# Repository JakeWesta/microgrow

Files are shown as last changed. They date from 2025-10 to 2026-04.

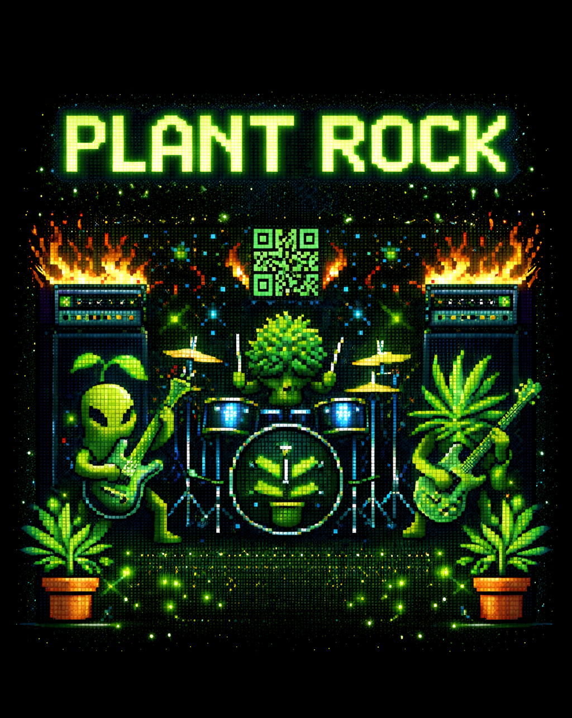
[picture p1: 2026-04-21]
app/assets/sprites/Rock_Poster.png

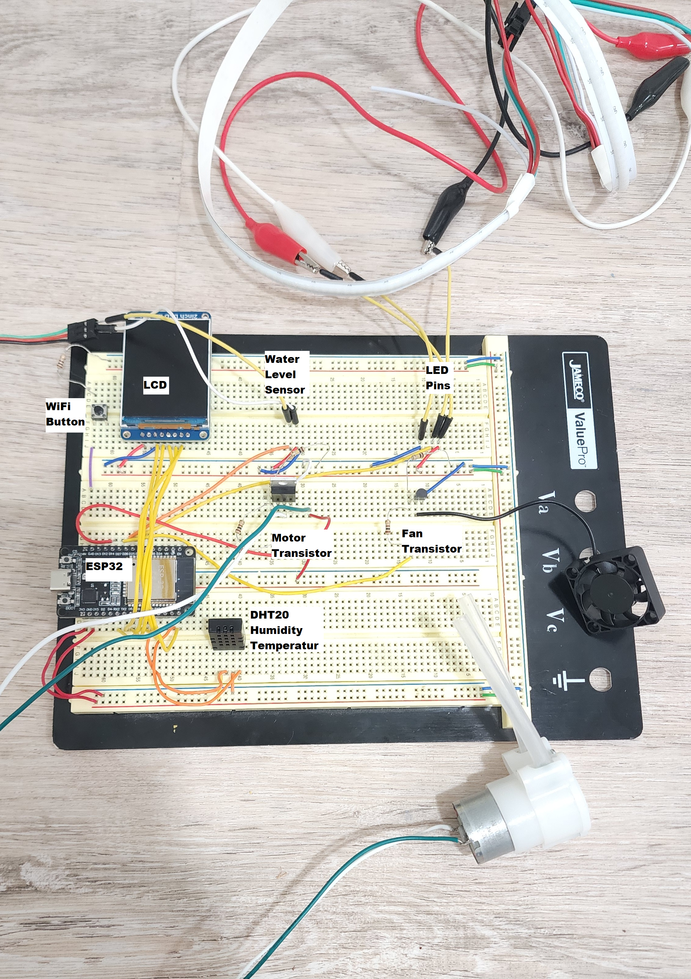
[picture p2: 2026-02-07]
Documentation/PCB 1.0/prototype_wiring_photo.png

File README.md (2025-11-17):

# Micro-Grow

- Flutter app demo video: https://www.youtube.com/watch?v=zIg6AqKC-sg

## Implemented Features:
### Pre-Alpha Build:
- **MQTT Connection** - Set up two-way communication between the ESP32 and the mobile app by using the MQTT protocol and EMQX broker.
- **Data Management** - Handle the storing of data by using a Hive database, which stores the watering cycle for each microgreen type.
- **Real-Time Sensor Data** - Configured ESP32 to poll readings from DHT11 temperature sensor and publishes the data every 5 seconds to the MQTT topic `microgrow/<habitatID>/sensor`.
- **User Interface** - Developed a Flutter app using Dart to allow the user to initialize and manage their MicroGrow habitat. Clicking on the habitat will display the real-time sensor data from the DHT11 on the app interface.

### Design Prototype:
- **Expanded Sensor Data** - Updated ESP32 code to publish sensor data for temperature/humidity, water level, and light intensity to MQTT topics `microgrow/<habitatID>/temp, humidity, water, light`. Sensor data is visible on the LCD screen to allow the user to easily monitor environmental conditions without their mobile device.
- **Expanded User Interface** - Updated dashboard to displays multiple created habitats and implemented the option to add and remove them. Selecting a habitat will display the real-time sensor data readings sent from the ESP32 for temperature, humidity, water level, and light intensity. Implemented the 'fun area' for the user to interact with their plant character
- **Schedule-Based Automation** - ESP32 pumps water from the water reservoir to the watering tray based on the watering schedule information sent during `microgrow/init`.
- **Manual Override** - Added a method for the user to control the water pump, fans, and light intensity manually from within the app. This feature does not interfere with the schedule timing.
- **Hardware** - Determined pin assignments for each electrical component. Connected ESP32, sensors, pump, lights, and LCD screen on a breadboard to test the functionality of each system. Designed CAD models to 3D-print the chassis and parts for the MicroGrow unit.

## Future Improvements:
- Include misting pump to regulate humidity within the habitat
- Create pixelated character sprites to display on the LCD screen
- Expand the 'fun area' in the mobile app to include customization features and scripted interaction between characters

## How to Use:

### Requirements:
- Flutter SDK
- Dart
- VS Code
- Arduino IDE
- Hive (for database)
- EMQX MQTT broker

### To setup the mobile application:
1. Ensure the required software is installed and install the necessary dependencies
2. Launch the mobile application:
   - Open VS Code and clone the repository
   - If prompted on VS Code, install the Flutter SDK and add to path if missing.
   - Install Flutter and Dart VS Code exstentions
   - Navigate to the app directory with `cd microgrow/app`
   - Fetch packages with `flutter pub get`
   - Connect to a 2.4 GHz WiFi network, such as a mobile hotspot
   - Start the application with `flutter run -d windows`
3. Flash the ESP32 firmware:
   - Open `main.ino` from the `ESP32 Firmware` directory in the Arduino IDE
   - Connect the ESP32 to a USB port on your computer
   - Follow the tutorial for the IDE to recognize the board: https://randomnerdtutorials.com/installing-the-esp32-board-in-arduino-ide-windows-instructions/
   - In Arduino IDE, select the correct configuration:
     - Board: ESP32 Dev Module
     - Port: auto-detected when plugging in
4. You may need to install the following packages. Easiest way is to go to the library manager tab on the left and search:
   - **PubSubClient** by Nick O'Leary
   - **DHT20** by Rob Tilaart
   - **ArduinoJson** by Benoit Blanchon
   - **Adafruit GFX Library** by Adafruit
   - **Adafruit ST7735 and ST7789 Library** by Adafruit
   - **FastLED** by Daniel Garcia
6. At the top of the code, assign the corresponding network information to the variables `ssid` and `password`
7. Press Upload and wait for flashing to complete

## Known Bugs:
- If sensor is unplugged, it displays garbage values. We don't handle that issue, as it displays more than 7 digits when disconnected from ESP32.
- If there is a disconnect from MQTT, we don't test for reconnection.
- Sometimes the ESP32 flashing will fail if its GPIO pins are connected to external peripherals/sensors. Remove the ESP32 from the breadboard before flashing to resolve this.
- Pump and fan will sometimes stop working during regular use.
- The current setup for the init sequence sends a JSON that is too large for the ESP32 to parse. This means that light scheduling is currently not being sent, as it had to be trimmed for the JSON to fit.

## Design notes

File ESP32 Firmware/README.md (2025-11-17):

# To run the ESP32 firmware:

1. Install the open-source Arduino IDE
2. Follow the tutorial for the IDE to recognize the board: https://randomnerdtutorials.com/installing-the-esp32-board-in-arduino-ide-windows-instructions/
3. Install the following packages. Easiest way is to go to the library manager tab on the left and search:
	
	PubSubClient by Nick O'Leary
	
	DHT20 by Rob Tilaart
	
	ArduinoJson by Benoit Blanchon
	
	Adafruit GFX Library by Adafruit
	
	Adafruit ST7735 and ST7789 Library by Adafruit
	
	FastLED by Daniel Garcia
4. Upload the firmware

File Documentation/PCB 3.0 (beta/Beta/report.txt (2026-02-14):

Info: Processing symbol 'DHT1:Connector_Molex:Molex_Micro-Fit_3.0_43650-0400_1x04_P3.00mm_Horizontal'.
Info: Processing symbol 'R1:Resistor_SMD:R_0201_0603Metric'.
Info: Processing symbol 'Q3:Package_TO_SOT_THT:TO-220-3_Vertical'.
Info: Processing symbol 'R3:Resistor_SMD:R_0201_0603Metric'.
Info: Processing symbol 'ST7789V1:Connector_Molex:Molex_Micro-Fit_3.0_43650-0600_1x06_P3.00mm_Horizontal'.
Info: Processing symbol 'Water_Level_Sensor1:Connector_Molex:Molex_Micro-Fit_3.0_43650-0300_1x03_P3.00mm_Horizontal'.
Info: Total warnings: 18, errors: 19.
Info: Processing symbol 'M1:Connector_Molex:Molex_Micro-Fit_3.0_43650-0215_1x02_P3.00mm_Vertical'.
Info: Processing symbol 'U1:esp32_devkit_v1_doit:esp32_devkit_v1_doit'.
Info: Processing symbol 'SW1:Connector_Molex:Molex_Micro-Fit_3.0_43650-0215_1x02_P3.00mm_Vertical'.
Info: Processing symbol 'Perilstatic_Pump1:Connector_Molex:Molex_Micro-Fit_3.0_43650-0215_1x02_P3.00mm_Vertical'.
Info: Processing symbol 'LED_STRIP1:Connector_Molex:Molex_Micro-Fit_3.0_43650-0300_1x03_P3.00mm_Horizontal'.
Info: Processing symbol 'Q1:Package_TO_SOT_THT:TO-220-3_Vertical'.
Info: Processing symbol 'R4:Resistor_SMD:R_0201_0603Metric'.
Info: Processing symbol 'R2:Resistor_SMD:R_0201_0603Metric'.
Added DHT1 (footprint 'Connector_Molex:Molex_Micro-Fit_3.0_43650-0400_1x04_P3.00mm_Horizontal').
Changed REF** reference designator to DHT1.
Changed DHT1 value from Molex_Micro-Fit_3.0_43650-0400_1x04_P3.00mm_Horizontal to ~.
Updated DHT1 symbol association from  to /6e4c08a4-b1cd-4914-aef5-b97c3696f05f.
Updated DHT1 sheetname to '/'.
Updated DHT1 sheetfile to 'prototype.kicad_sch'.
Updated Water_Level_Sensor1 sheetname to '/'.
Updated Water_Level_Sensor1 sheetfile to 'prototype.kicad_sch'.

Added LED_STRIP1 (footprint 'Connector_Molex:Molex_Micro-Fit_3.0_43650-0300_1x03_P3.00mm_Horizontal').
Changed REF** reference designator to LED_STRIP1.
Changed LED_STRIP1 value from Molex_Micro-Fit_3.0_43650-0300_1x03_P3.00mm_Horizontal to ~.
Updated LED_STRIP1 symbol association from  to /8e498da7-6c69-4450-a1d9-924dce50ed07.
Updated LED_STRIP1 sheetname to '/'.
Updated LED_STRIP1 sheetfile to 'prototype.kicad_sch'.
Changed REF** reference designator to Water_Level_Sensor1.
Added M1 (footprint 'Connector_Molex:Molex_Micro-Fit_3.0_43650-0215_1x02_P3.00mm_Vertical').
Changed REF** reference designator to M1.
Changed M1 value from Molex_Micro-Fit_3.0_43650-0215_1x02_P3.00mm_Vertical to Fan.
Updated M1 symbol association from  to /a24ab250-104e-40cc-be6c-cd05863d6f31.
Updated M1 fields.
Updated M1 sheetname to '/'.
Updated M1 sheetfile to 'prototype.kicad_sch'.
Add net /FAN_NEG.
Connected M1 pin 2 to /FAN_NEG.
Add net VCC.
Connected M1 pin 1 to VCC.
Added Perilstatic_Pump1 (footprint 'Connector_Molex:Molex_Micro-Fit_3.0_43650-0215_1x02_P3.00mm_Vertical').
Changed REF** reference designator to Perilstatic_Pump1.
Changed Perilstatic_Pump1 value from Molex_Micro-Fit_3.0_43650-0215_1x02_P3.00mm_Vertical to ~.
Updated Perilstatic_Pump1 symbol association from  to /13c4dc11-f264-4864-8656-4de5b2fcf814.
Updated Perilstatic_Pump1 sheetname to '/'.
Updated Perilstatic_Pump1 sheetfile to 'prototype.kicad_sch'.
Added Q1 (footprint 'Package_TO_SOT_THT:TO-220-3_Vertical').
Changed REF** reference designator to Q1.
Changed Q1 value from TO-220-3_Vertical to IRLB8721PBF.
Updated Q1 symbol association from  to /b185a6f1-6a33-459d-a671-ce34d81b2ea3.
Updated Q1 fields.
Updated Q1 sheetname to '/'.
Updated Q1 sheetfile to 'prototype.kicad_sch'.
Updated Q1 footprint filters to 'TO?220*'.
Add net GND.
Connected Q1 pin 3 to GND.
Add net /PUMP_NEG.
Connected Q1 pin 2 to /PUMP_NEG.
Add net Net-(Q1-G).
Connected Q1 pin 1 to Net-(Q1-G).
Updated M1 footprint filters to 'PinHeader*P2.54mm* TerminalBlock*'.
Added Q3 (footprint 'Package_TO_SOT_THT:TO-220-3_Vertical').
Changed REF** reference designator to Q3.
Changed Q3 value from TO-220-3_Vertical to IRLB8721PBF.
Updated Q3 symbol association from  to /fbe2aa08-65bc-4db5-b509-0606b8fdc2ba.
Updated Q3 fields.
Updated Q3 sheetname to '/'.
Updated Q3 sheetfile to 'prototype.kicad_sch'.
Updated Q3 footprint filters to 'TO?220*'.
Add net Net-(Q3-G).
Connected Q3 pin 1 to Net-(Q3-G).
Connected Q3 pin 2 to /FAN_NEG.
Connected Q3 pin 3 to GND.
Added R1 (footprint 'Resistor_SMD:R_0201_0603Metric').
Changed REF** reference designator to R1.
Changed R1 value from R_0201_0603Metric to 100.
Updated R1 symbol association from  to /6cbc41ab-6199-446f-b66f-0273e11d1e1b.
Updated R1 fields.
Updated R1 sheetname to '/'.
Updated R1 sheetfile to 'prototype.kicad_sch'.
Updated R1 footprint filters to 'R_*'.
Add net /PUMP.
Connected R1 pin 2 to /PUMP.
Connected R1 pin 1 to Net-(Q1-G).
Added R2 (footprint 'Resistor_SMD:R_0201_0603Metric').
Changed REF** reference designator to R2.
Changed R2 value from R_0201_0603Metric to 100k.
Updated R2 symbol association from  to /58fef6ab-5448-4966-9282-118c6e4f16f3.
Updated R2 sheetname to '/'.
Updated R2 sheetfile to 'prototype.kicad_sch'.
Updated R2 footprint filters to 'R_*'.
Connected R2 pin 1 to GND.
Connected R2 pin 2 to Net-(Q1-G).
Added R3 (footprint 'Resistor_SMD:R_0201_0603Metric').
Changed REF** reference designator to R3.
Changed R3 value from R_0201_0603Metric to 100.
Updated R3 symbol association from  to /cc2fe59e-3a58-4862-b4cd-096af761090b.
Updated R3 fields.
Updated R3 sheetname to '/'.
Updated R3 sheetfile to 'prototype.kicad_sch'.
Updated R3 footprint filters to 'R_*'.
Connected R3 pin 2 to Net-(Q3-G).
Add net /FAN.
Connected R3 pin 1 to /FAN.
Added R4 (footprint 'Resistor_SMD:R_0201_0603Metric').
Changed REF** reference designator to R4.
Changed R4 value from R_0201_0603Metric to 100k.
Updated R4 symbol association from  to /ef9e54ad-bc10-445a-8cc7-7e4a79940005.
Updated R4 fields.
Updated R4 sheetname to '/'.
Updated R4 sheetfile to 'prototype.kicad_sch'.
Updated R4 footprint filters to 'R_*'.
Connected R4 pin 2 to GND.
Connected R4 pin 1 to Net-(Q3-G).
Updated R2 fields.
Added ST7789V1 (footprint 'Connector_Molex:Molex_Micro-Fit_3.0_43650-0600_1x06_P3.00mm_Horizontal').
Changed REF** reference designator to ST7789V1.
Changed ST7789V1 value from Molex_Micro-Fit_3.0_43650-0600_1x06_P3.00mm_Horizontal to ~.
Updated ST7789V1 symbol association from  to /6443309b-f941-4119-b5bf-95145ad43db5.
Updated ST7789V1 sheetname to '/'.
Updated ST7789V1 sheetfile to 'prototype.kicad_sch'.
Added SW1 (footprint 'Connector_Molex:Molex_Micro-Fit_3.0_43650-0215_1x02_P3.00mm_Vertical').
Changed REF** reference designator to SW1.
Changed SW1 value from Molex_Micro-Fit_3.0_43650-0215_1x02_P3.00mm_Vertical to SW_Push.
Updated SW1 symbol association from  to /d7c7dc86-ded3-42bf-bfc8-d6a93b28d2ff.
Updated SW1 fields.
Updated SW1 sheetname to '/'.
Updated SW1 sheetfile to 'prototype.kicad_sch'.
Add net /WiFi_BUTTON.
Connected SW1 pin 1 to /WiFi_BUTTON.
Connected SW1 pin 2 to GND.
Added U1 (footprint 'esp32_devkit_v1_doit:esp32_devkit_v1_doit').
Changed REF** reference designator to U1.
Changed U1 value from ESP32-DevKit-V1-DOIT to ESP32-DEVKIT-V1.
Updated U1 symbol association from  to /7857917b-6d23-4520-a81d-1aefb2627a26.
Updated U1 fields.
Updated U1 sheetname to '/'.
Updated U1 sheetfile to 'prototype.kicad_sch'.
Add net /LCD_DC.
Connected U1 pin 6 to /LCD_DC.
Add net /DHT_SDA.
Connected U1 pin 11 to /DHT_SDA.
Add net +3V3.
Connected U1 pin 30 to +3V3.
Add net /LCD_CLK.
Connected U1 pin 9 to /LCD_CLK.
Add net unconnected-(U1-D4-Pad5).
Connected U1 pin 5 to unconnected-(U1-D4-Pad5).
Add net /LCD_RST.
Connected U1 pin 7 to /LCD_RST.
Connected U1 pin 1 to VCC.
Add net /LED_STRIP.
Connected U1 pin 25 to /LED_STRIP.
Add net unconnected-(U1-D33-Pad22).
Connected U1 pin 22 to unconnected-(U1-D33-Pad22).
Add net /WATER_LEV.
Connected U1 pin 26 to /WATER_LEV.
Connected U1 pin 2 to GND.
Add net unconnected-(U1-D35-Pad20).
Connected U1 pin 20 to unconnected-(U1-D35-Pad20).
Add net unconnected-(U1-D34-Pad19).
Connected U1 pin 19 to unconnected-(U1-D34-Pad19).
Connected U1 pin 29 to GND.
Add net unconnected-(U1-VP-Pad17).
Connected U1 pin 17 to unconnected-(U1-VP-Pad17).
Connected U1 pin 13 to unconnected-(U1-TX0-Pad13).
Add net unconnected-(U1-D25-Pad23).
Connected U1 pin 23 to unconnected-(U1-D25-Pad23).
Connected U1 pin 24 to /FAN.
Add net unconnected-(U1-EN-Pad16).
Connected U1 pin 16 to unconnected-(U1-EN-Pad16).
Add net unconnected-(U1-D19-Pad10).
Connected U1 pin 10 to unconnected-(U1-D19-Pad10).
Add net unconnected-(U1-VN-Pad18).
Connected U1 pin 18 to unconnected-(U1-VN-Pad18).
Add net /LCD_CS.
Connected U1 pin 8 to /LCD_CS.
Add net /LCD_DIN.
Connected U1 pin 15 to /LCD_DIN.
Add net unconnected-(U1-D13-Pad28).
Connected U1 pin 28 to unconnected-(U1-D13-Pad28).
Add net unconnected-(U1-D12-Pad27).
Connected U1 pin 27 to unconnected-(U1-D12-Pad27).
Add net unconnected-(U1-RX0-Pad12).
Connected U1 pin 12 to unconnected-(U1-RX0-Pad12).
Connected U1 pin 21 to /PUMP.
Add net /DHT_SCL.
Connected U1 pin 14 to /DHT_SCL.
Connected U1 pin 4 to /WiFi_BUTTON.
Add net unconnected-(U1-D15-Pad3).
Connected U1 pin 3 to unconnected-(U1-D15-Pad3).
Added Water_Level_Sensor1 (footprint 'Connector_Molex:Molex_Micro-Fit_3.0_43650-0300_1x03_P3.00mm_Horizontal').
Add net unconnected-(U1-TX0-Pad13).
Changed Water_Level_Sensor1 value from Molex_Micro-Fit_3.0_43650-0300_1x03_P3.00mm_Horizontal to ~.
Updated Water_Level_Sensor1 symbol association from  to /28ca019c-f3e1-41e0-b59c-fe60d403124b.
Warning: No net found for component DHT1 pad 4 (no pin 4 in symbol).
Warning: No net found for component DHT1 pad 3 (no pin 3 in symbol).
Warning: No net found for component DHT1 pad 1 (no pin 1 in symbol).
Warning: No net found for component DHT1 pad 2 (no pin 2 in symbol).
Warning: No net found for component LED_STRIP1 pad 3 (no pin 3 in symbol).
Warning: No net found for component LED_STRIP1 pad 2 (no pin 2 in symbol).
Warning: No net found for component LED_STRIP1 pad 1 (no pin 1 in symbol).
Warning: No net found for component ST7789V1 pad 2 (no pin 2 in symbol).
Warning: No net found for component Perilstatic_Pump1 pad 1 (no pin 1 in symbol).
Warning: No net found for component ST7789V1 pad 5 (no pin 5 in symbol).
Warning: No net found for component ST7789V1 pad 1 (no pin 1 in symbol).
Warning: No net found for component ST7789V1 pad 6 (no pin 6 in symbol).
Warning: No net found for component Water_Level_Sensor1 pad 2 (no pin 2 in symbol).
Warning: No net found for component Water_Level_Sensor1 pad 1 (no pin 1 in symbol).
Warning: No net found for component Water_Level_Sensor1 pad 3 (no pin 3 in symbol).
Warning: No net found for component ST7789V1 pad 4 (no pin 4 in symbol).
Warning: No net found for component Perilstatic_Pump1 pad 2 (no pin 2 in symbol).
Warning: No net found for component ST7789V1 pad 3 (no pin 3 in symbol).
Error: Symbol DHT1 has pins with no number.  These pins can not be matched to pads in Connector_Molex:Molex_Micro-Fit_3.0_43650-0400_1x04_P3.00mm_Horizontal.
Error: Symbol DHT1 has pins with no number.  These pins can not be matched to pads in Connector_Molex:Molex_Micro-Fit_3.0_43650-0400_1x04_P3.00mm_Horizontal.
Error: Symbol DHT1 has pins with no number.  These pins can not be matched to pads in Connector_Molex:Molex_Micro-Fit_3.0_43650-0400_1x04_P3.00mm_Horizontal.
Error: Symbol LED_STRIP1 has pins with no number.  These pins can not be matched to pads in Connector_Molex:Molex_Micro-Fit_3.0_43650-0300_1x03_P3.00mm_Horizontal.
Error: Symbol Perilstatic_Pump1 has pins with no number.  These pins can not be matched to pads in Connector_Molex:Molex_Micro-Fit_3.0_43650-0215_1x02_P3.00mm_Vertical.
Error: Symbol Perilstatic_Pump1 has pins with no number.  These pins can not be matched to pads in Connector_Molex:Molex_Micro-Fit_3.0_43650-0215_1x02_P3.00mm_Vertical.
Error: Symbol ST7789V1 has pins with no number.  These pins can not be matched to pads in Connector_Molex:Molex_Micro-Fit_3.0_43650-0600_1x06_P3.00mm_Horizontal.
Error: Symbol ST7789V1 has pins with no number.  These pins can not be matched to pads in Connector_Molex:Molex_Micro-Fit_3.0_43650-0600_1x06_P3.00mm_Horizontal.
Error: Symbol ST7789V1 has pins with no number.  These pins can not be matched to pads in Connector_Molex:Molex_Micro-Fit_3.0_43650-0600_1x06_P3.00mm_Horizontal.
Error: Symbol ST7789V1 has pins with no number.  These pins can not be matched to pads in Connector_Molex:Molex_Micro-Fit_3.0_43650-0600_1x06_P3.00mm_Horizontal.
Error: Symbol ST7789V1 has pins with no number.  These pins can not be matched to pads in Connector_Molex:Molex_Micro-Fit_3.0_43650-0600_1x06_P3.00mm_Horizontal.
Error: Symbol ST7789V1 has pins with no number.  These pins can not be matched to pads in Connector_Molex:Molex_Micro-Fit_3.0_43650-0600_1x06_P3.00mm_Horizontal.
Error: Symbol ST7789V1 has pins with no number.  These pins can not be matched to pads in Connector_Molex:Molex_Micro-Fit_3.0_43650-0600_1x06_P3.00mm_Horizontal.
Error: Symbol Water_Level_Sensor1 has pins with no number.  These pins can not be matched to pads in Connector_Molex:Molex_Micro-Fit_3.0_43650-0300_1x03_P3.00mm_Horizontal.
Error: Symbol Water_Level_Sensor1 has pins with no number.  These pins can not be matched to pads in Connector_Molex:Molex_Micro-Fit_3.0_43650-0300_1x03_P3.00mm_Horizontal.
Error: Symbol Water_Level_Sensor1 has pins with no number.  These pins can not be matched to pads in Connector_Molex:Molex_Micro-Fit_3.0_43650-0300_1x03_P3.00mm_Horizontal.
Error: Symbol LED_STRIP1 has pins with no number.  These pins can not be matched to pads in Connector_Molex:Molex_Micro-Fit_3.0_43650-0300_1x03_P3.00mm_Horizontal.
Error: Symbol LED_STRIP1 has pins with no number.  These pins can not be matched to pads in Connector_Molex:Molex_Micro-Fit_3.0_43650-0300_1x03_P3.00mm_Horizontal.
Error: Symbol DHT1 has pins with no number.  These pins can not be matched to pads in Connector_Molex:Molex_Micro-Fit_3.0_43650-0400_1x04_P3.00mm_Horizontal.

Info: Total warnings: 18, errors: 19.

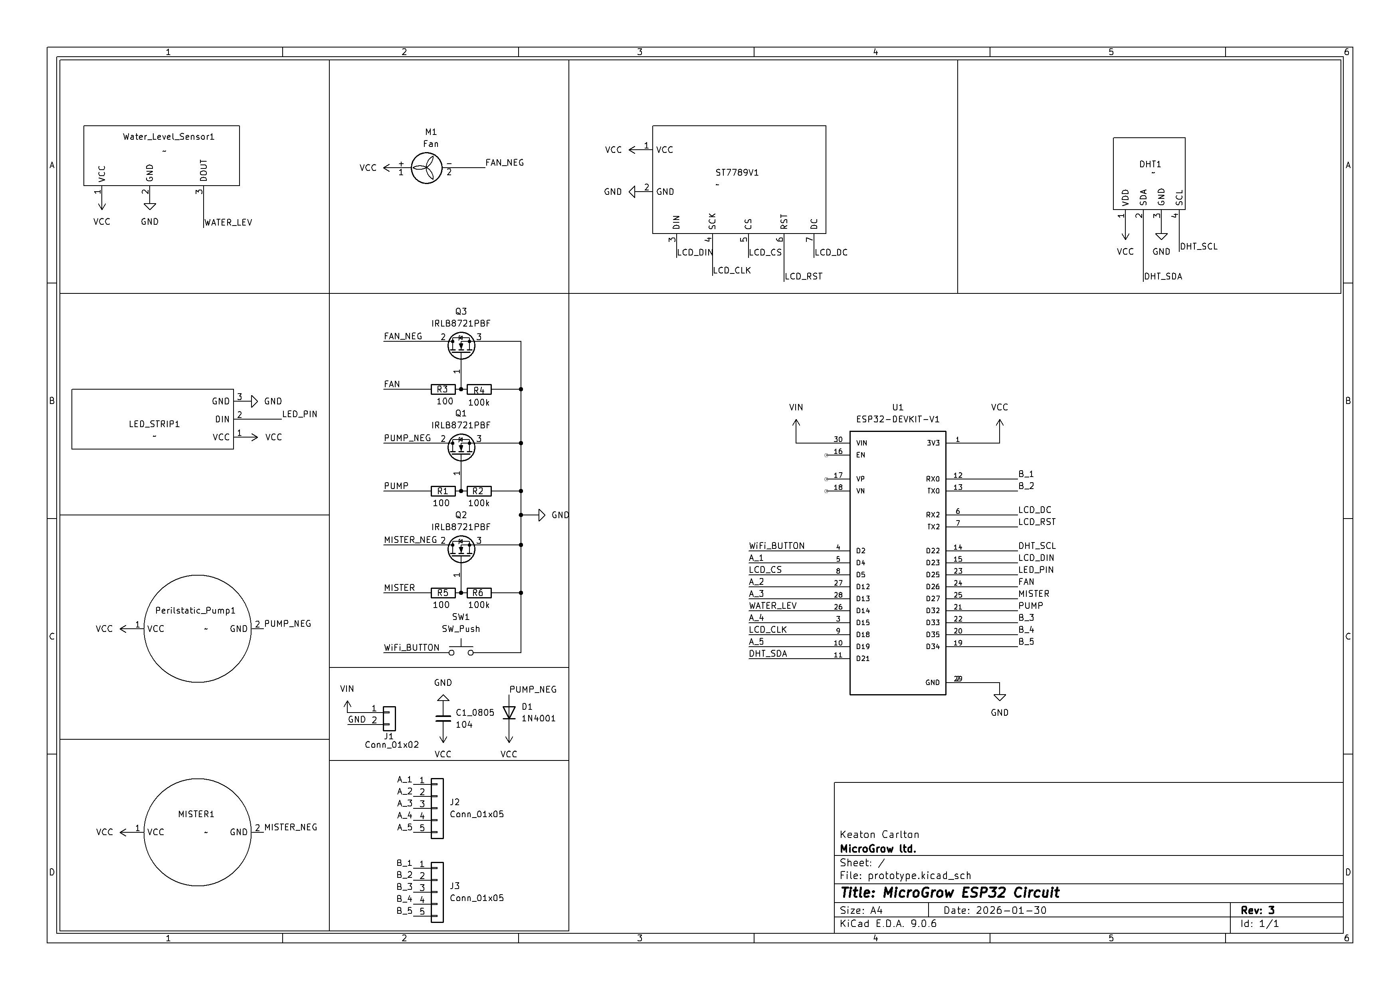
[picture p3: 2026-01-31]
Documentation/PCB 1.0/schematic_photo.png

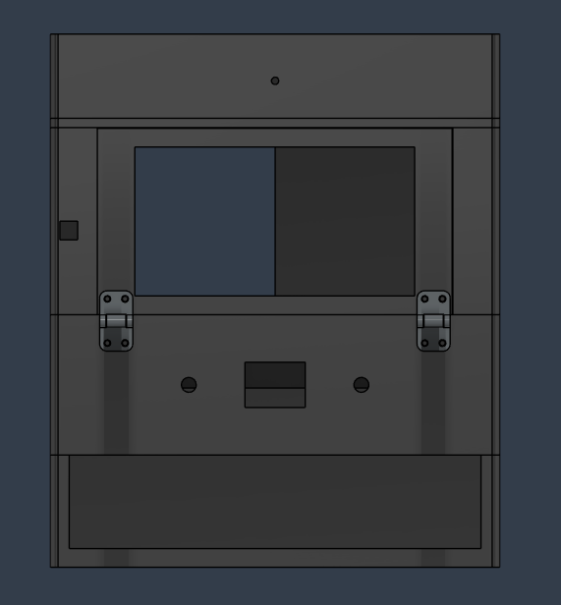
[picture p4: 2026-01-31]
Physical Design/Final Front View.PNG

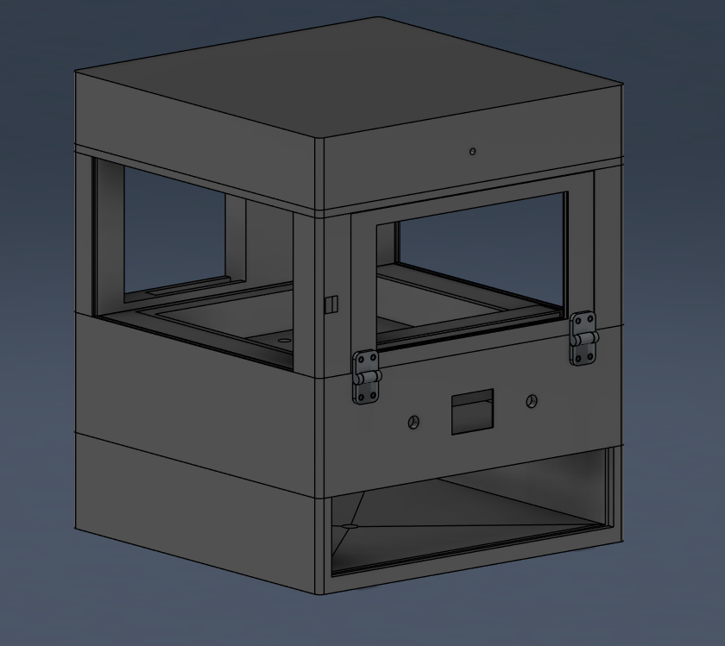
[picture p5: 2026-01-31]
Physical Design/Final Ortho View.PNG

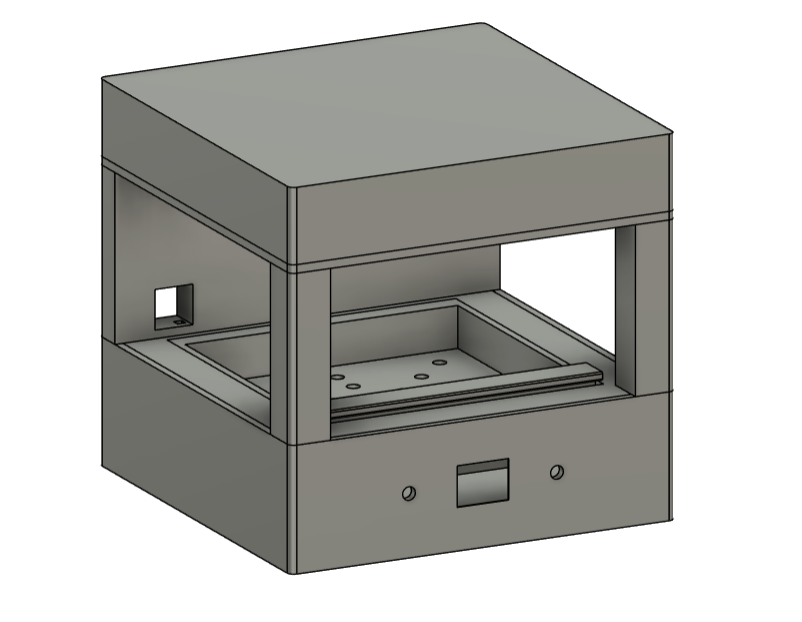
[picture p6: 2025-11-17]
Physical Design/MicroGrow 3D Model.png

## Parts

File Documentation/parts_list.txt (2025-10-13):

https://docs.google.com/spreadsheets/d/1zEimQMvjbTs6dZiR2b9LwuBSMXzHEefUJ1ij9qsu0_o/edit?usp=sharing

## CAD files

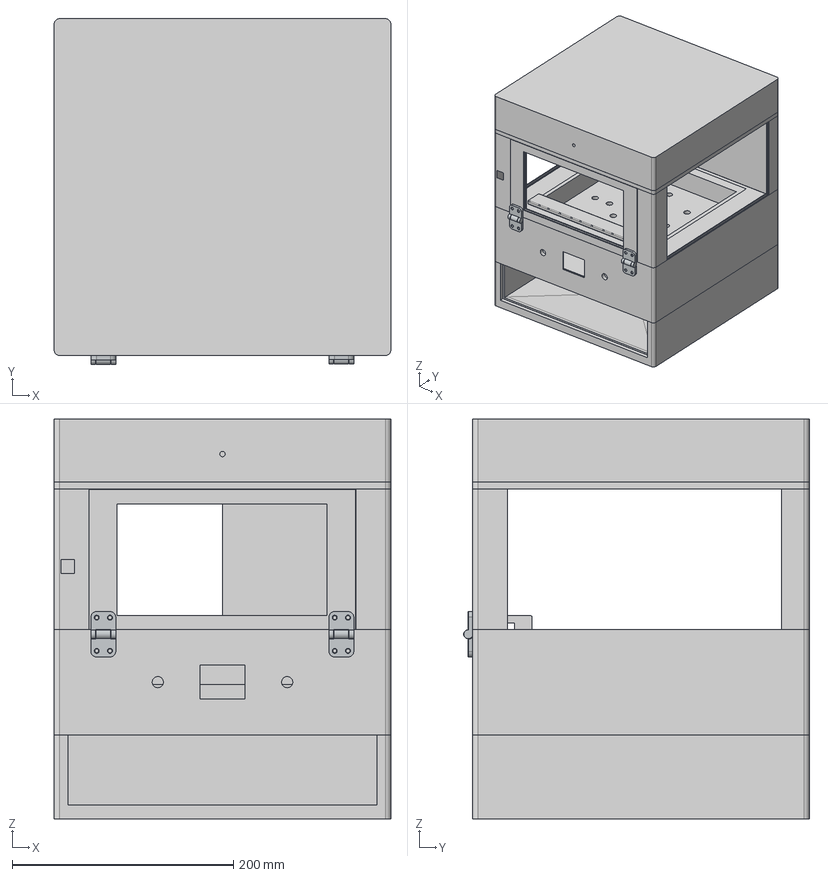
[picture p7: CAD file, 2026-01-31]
Physical Design/Final Assembly.step
304.8 x 312.9 x 362.0 mm

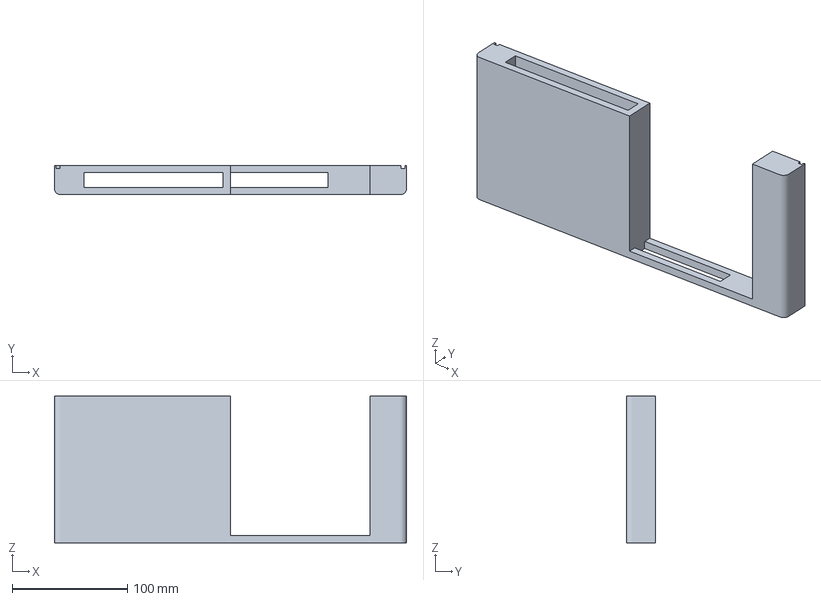
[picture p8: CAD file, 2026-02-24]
Physical Design/Back Plate V1.3mf
304.8 x 25.4 x 127.0 mm

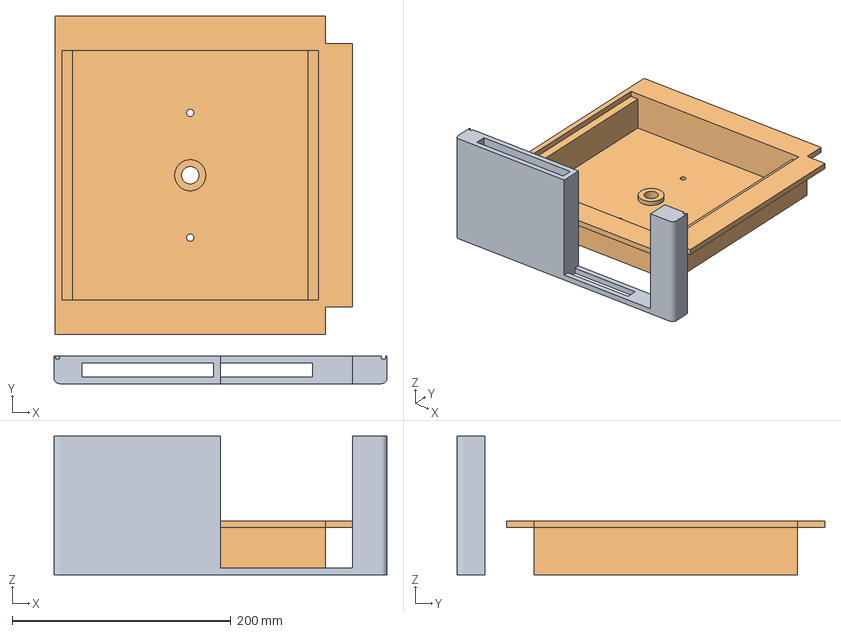
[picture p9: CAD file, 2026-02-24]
Physical Design/weekend vibe.3mf
304.8 x 336.4 x 127.0 mm
Back Plate V1.stl
Water Holder V1.stl

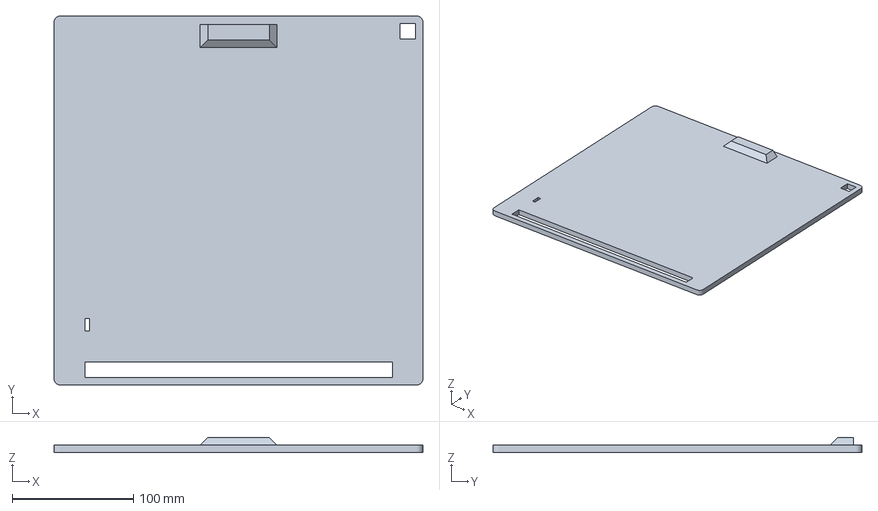
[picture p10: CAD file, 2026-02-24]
Physical Design/Roof Base V1.3mf
304.8 x 304.8 x 12.7 mm

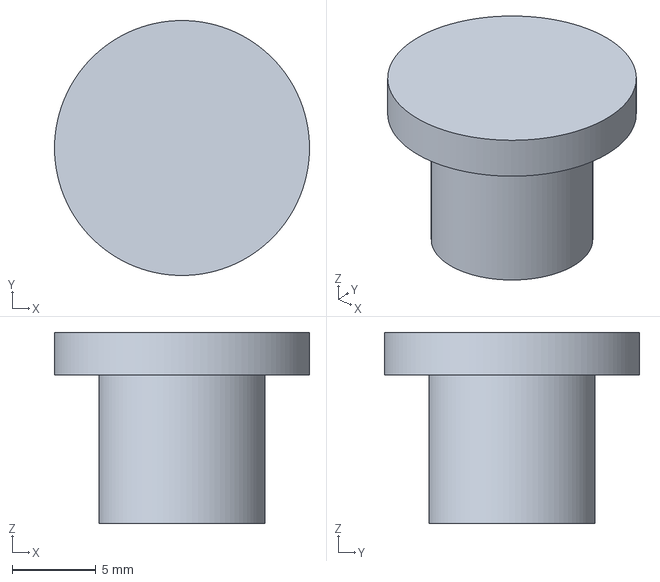
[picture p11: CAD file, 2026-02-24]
Physical Design/TEST.3mf
15.2 x 15.2 x 11.4 mm

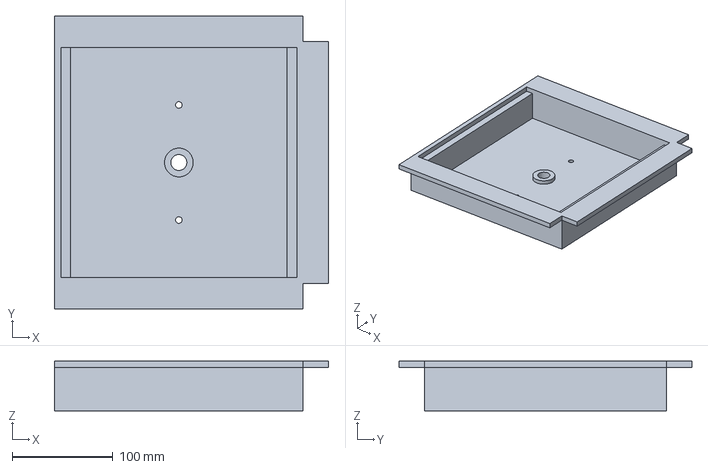
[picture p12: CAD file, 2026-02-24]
Physical Design/Water Holder V1.3mf
272.3 x 291.1 x 49.5 mm

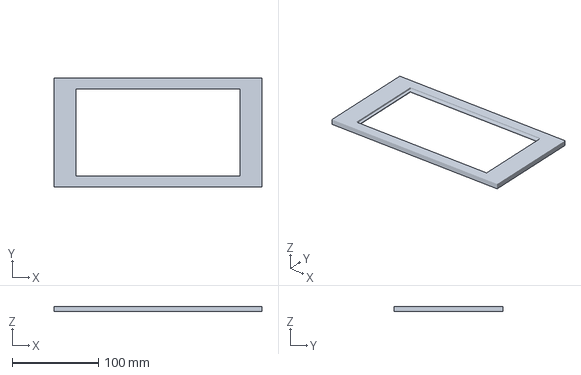
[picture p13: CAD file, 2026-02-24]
Physical Design/Front Door V1.3mf
240.8 x 126.5 x 6.35 mm

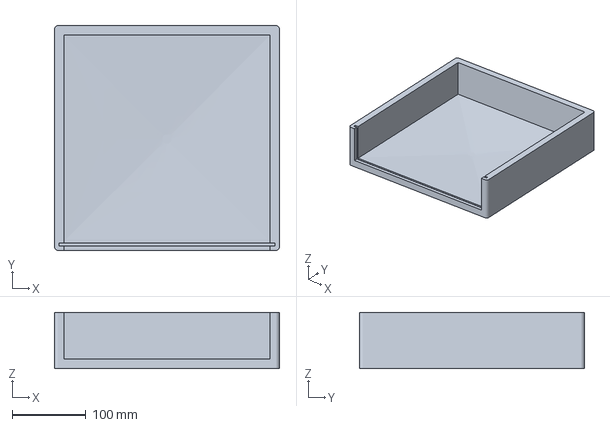
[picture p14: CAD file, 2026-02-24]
Physical Design/Water Reservoir.3mf
304.8 x 304.8 x 76.2 mm

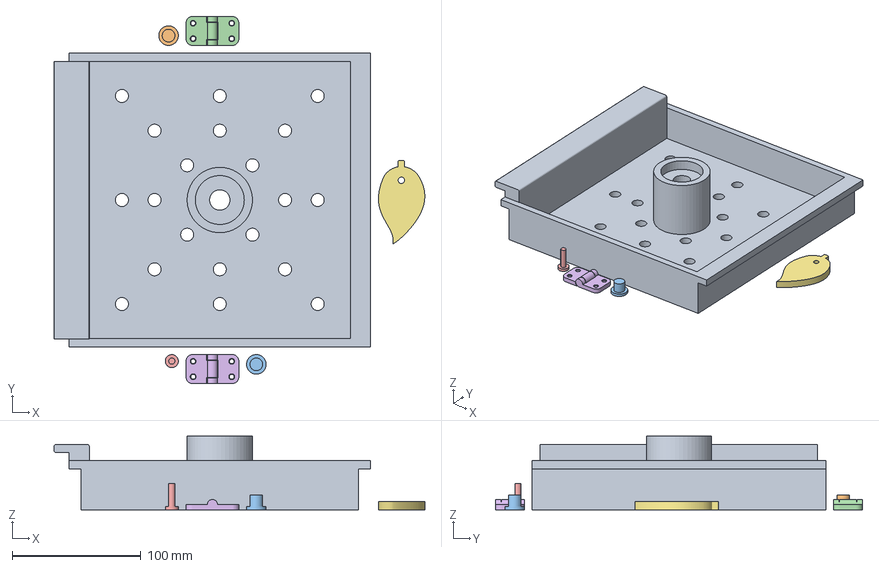
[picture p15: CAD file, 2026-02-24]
Physical Design/Soil Holder V1.3mf
288.2 x 285.3 x 57.2 mm
Soil Holder V1.stl
Buttons V1.stl x 2
Hinge_PrintInPlaceV2_VC.stl x 2
Leaf Holder V1.stl
Leaf Door Holder V1.stl

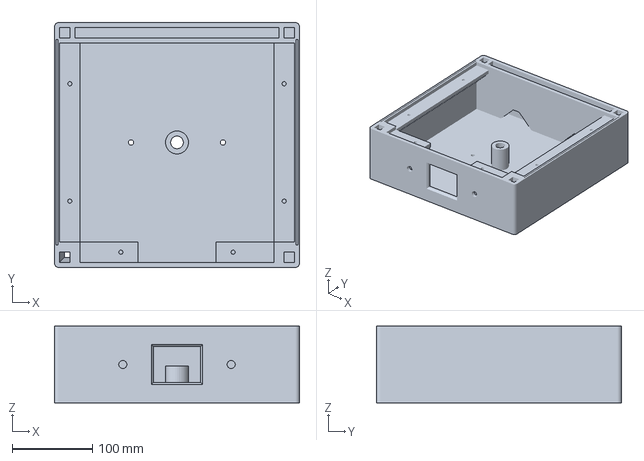
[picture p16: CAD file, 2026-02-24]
Physical Design/Base.3mf
304.8 x 304.8 x 95.2 mm

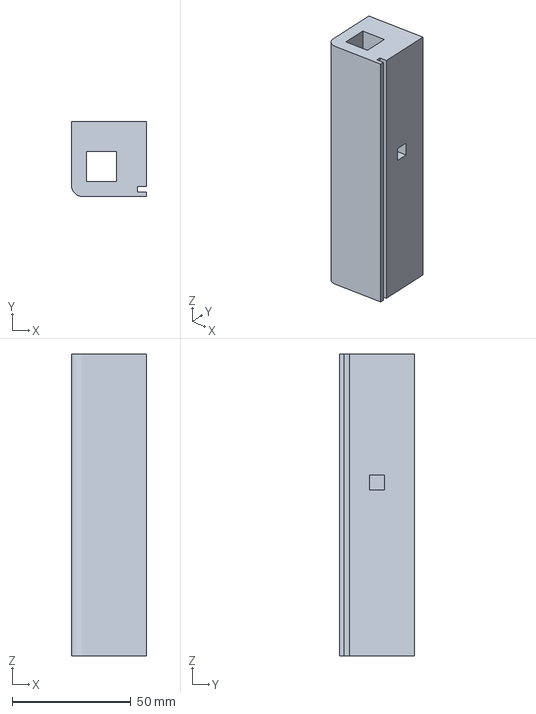
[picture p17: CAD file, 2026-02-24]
Physical Design/Right Arm V1.3mf
31.8 x 31.8 x 127.0 mm

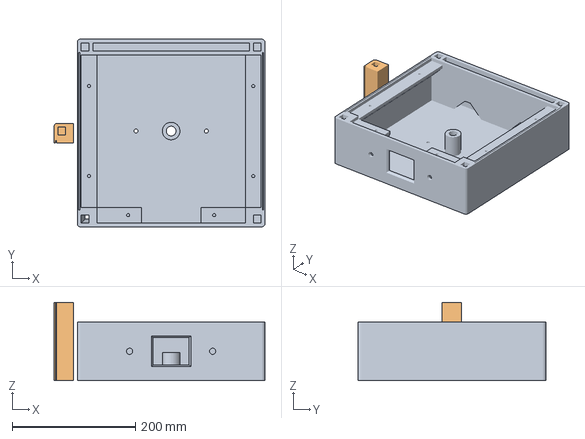
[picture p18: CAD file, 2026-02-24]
Physical Design/base + left ram.3mf
342.5 x 304.8 x 127.0 mm
Base Component V1.stl
Left Arm V1.stl

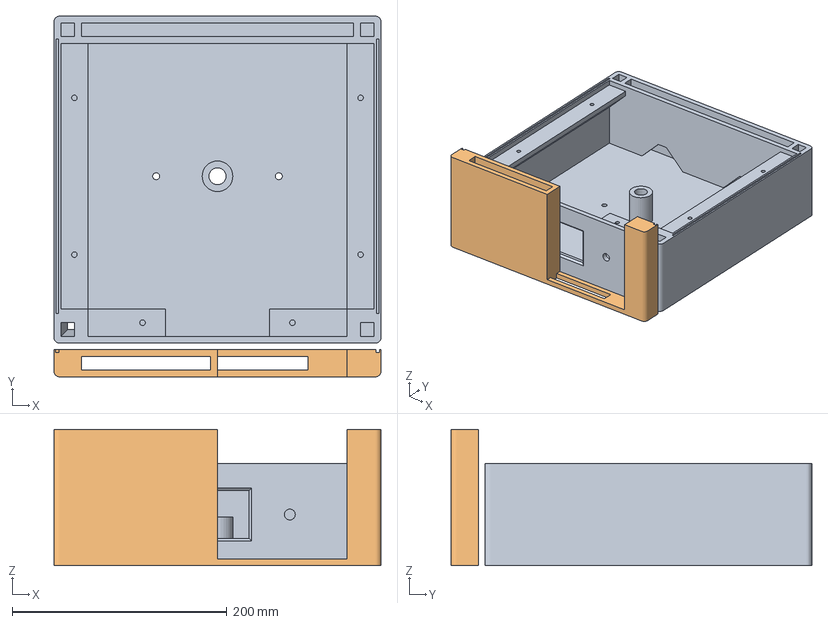
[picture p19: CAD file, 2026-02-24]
Physical Design/Weekend goat.3mf
304.8 x 336.2 x 127.0 mm
Base Component V1.stl
Back Plate V1.stl

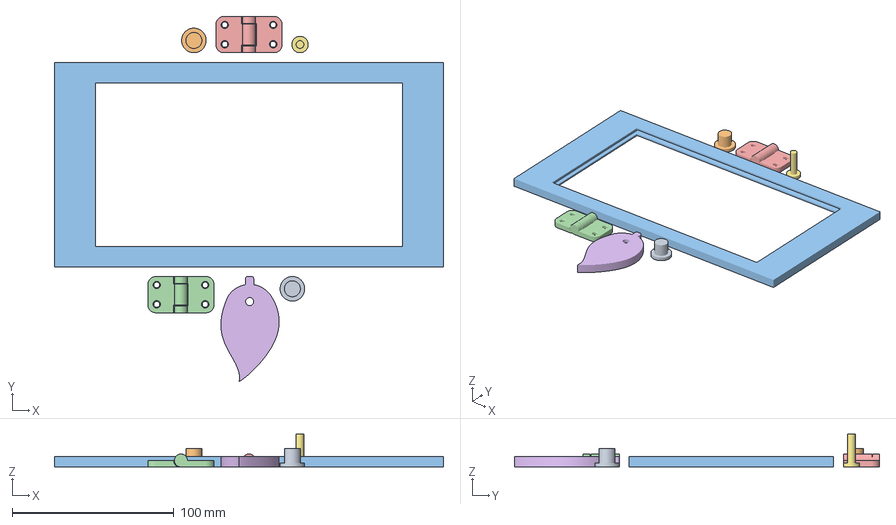
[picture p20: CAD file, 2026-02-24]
Physical Design/all da lil stuff.3mf
240.8 x 226.1 x 20.3 mm
Buttons V1.stl x 2
Front Door V1.stl
Hinge_PrintInPlaceV2_VC.stl x 2
Leaf Door Holder V1.stl
Leaf Holder V1.stl

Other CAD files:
Physical Design/Leaf Holder V1.stl
Physical Design/Buttons V1.stl
Physical Design/Leaf Door Holder V1.stl
Physical Design/Base Component V1.stl
Physical Design/Back Plate V1.stl
Physical Design/Front DoorV1.stl
Physical Design/Hinge_PrintInPlaceV2_VC.stl
Physical Design/Left Arm V1.stl
Physical Design/Right Arm V1.stl
Physical Design/Roof Base V1.stl
Physical Design/Roof Top V1.stl
Physical Design/Soil Holder V1.stl
Physical Design/Water Holder V1.stl
Physical Design/Water Reservoir V1.stl

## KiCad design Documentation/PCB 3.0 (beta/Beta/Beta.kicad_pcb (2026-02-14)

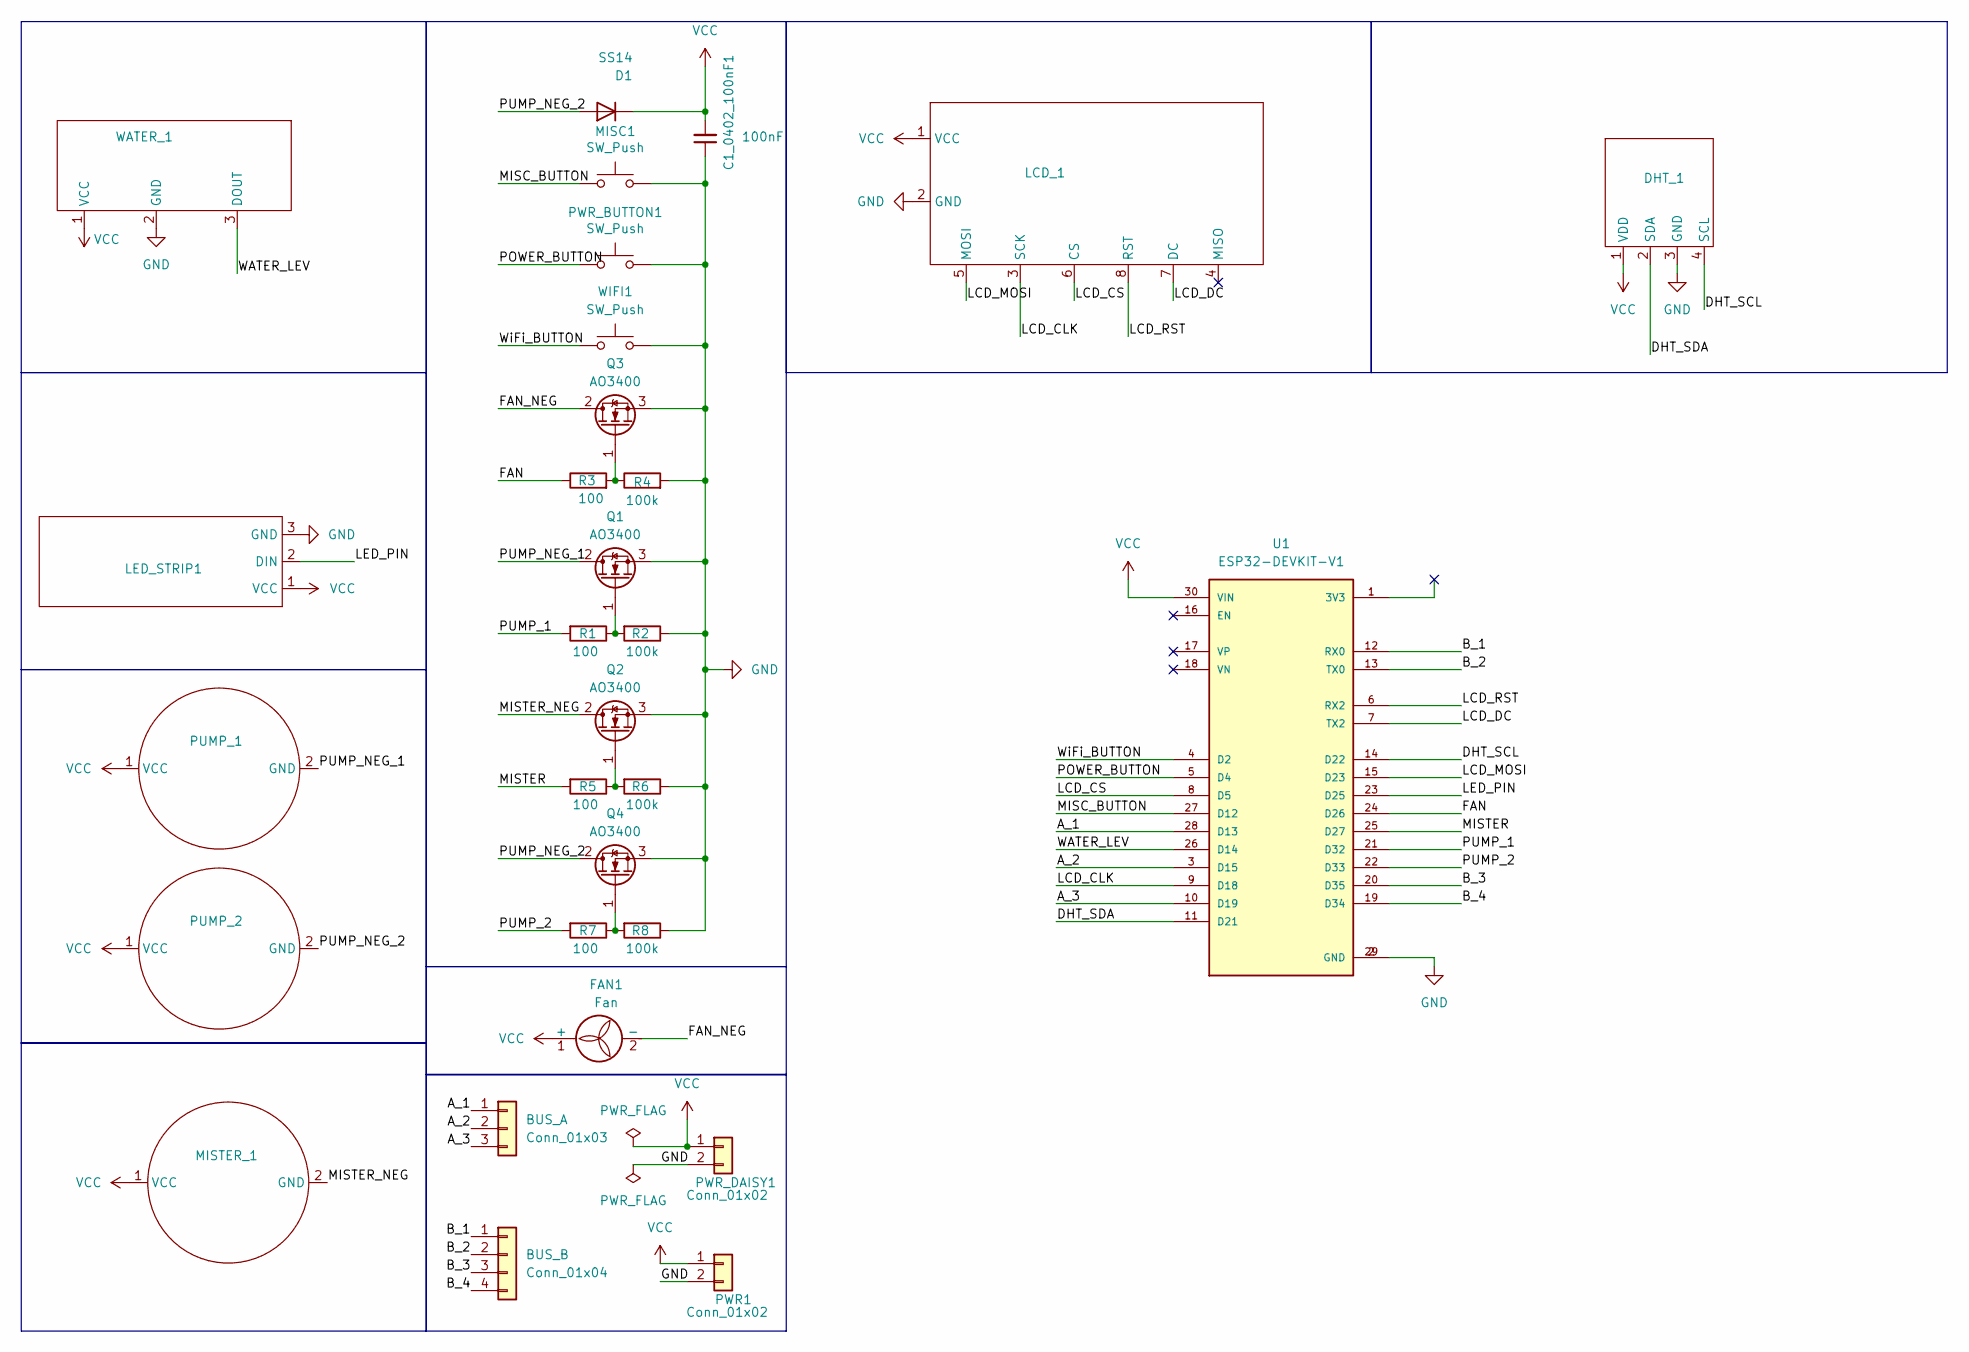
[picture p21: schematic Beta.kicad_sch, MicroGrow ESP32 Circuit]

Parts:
BUS_A: Conn_01x03; PinHeader_1x03_P1.00mm_Vertical
BUS_B: Conn_01x04; PinHeader_1x04_P1.00mm_Vertical
C1_0402_100nF1: 100nF; C_0402_1005Metric
D1: SS14; D_SOD-123
DHT_1: JST_PH_B4B-PH-K_1x04_P2.00mm_Vertical
FAN1: Fan; JST_PH_B2B-PH-K_1x02_P2.00mm_Vertical
LCD_1: 1x08(2 and 6) vertical JST PH
LED_STRIP1: JST_PH_B3B-PH-K_1x03_P2.00mm_Vertical
MISC1: SW_Push; JST_PH_B2B-PH-K_1x02_P2.00mm_Vertical
MISTER_1: JST_PH_B2B-PH-K_1x02_P2.00mm_Vertical
PUMP_1, PUMP_2: JST_PH_B2B-PH-K_1x02_P2.00mm_Vertical
PWR1: Conn_01x02; JST_VH_B2P-VH_1x02_P3.96mm_Vertical
PWR_BUTTON1: SW_Push; JST_PH_B2B-PH-K_1x02_P2.00mm_Vertical
PWR_DAISY1: Conn_01x02; JST_VH_B2P-VH_1x02_P3.96mm_Vertical
Q1, Q2, Q3, Q4: AO3400; SOT-23
R1, R3, R5, R7: 100; R_0402_1005Metric
R2, R4, R6, R8: 100k; R_0402_1005Metric
U1: ESP32-DEVKIT-V1; ESP32-C3-DevKitM-1; PARTREV N/A
WATER_1: JST_PH_B3B-PH-K_1x03_P2.00mm_Vertical
WIFI1: SW_Push; JST_PH_B2B-PH-K_1x02_P2.00mm_Vertical

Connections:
/A_1: BUS_A.1, U1.28 (D13); also elsewhere on the board
/A_2: BUS_A.2, U1.3 (D15); also elsewhere on the board
/A_3: BUS_A.3, U1.10 (D19); also elsewhere on the board
/B_1: BUS_B.1, U1.12 (RX0); also elsewhere on the board
/B_2: BUS_B.2, U1.13 (TX0); also elsewhere on the board
/B_3: BUS_B.3, U1.20 (D35); also elsewhere on the board
/B_4: BUS_B.4, U1.19 (D34); also elsewhere on the board
/DHT_SCL: DHT_1.4 (SCL), U1.14 (D22)
/DHT_SDA: DHT_1.2 (SDA), U1.11 (D21)
/FAN: R3.1, U1.24 (D26)
/FAN_NEG: FAN1.2 (-), Q3.2 (D)
/LCD_CLK: LCD_1.3 (SCK), U1.9 (D18)
/LCD_CS: LCD_1.6 (CS), U1.8 (D5)
/LCD_DC: LCD_1.7 (DC), U1.7 (TX2)
/LCD_MOSI: LCD_1.5 (MOSI), U1.15 (D23)
/LCD_RST: LCD_1.8 (RST), U1.6 (RX2)
/LED_PIN: LED_STRIP1.2 (DIN), U1.23 (D25)
/MISC_BUTTON: MISC1.1, U1.27 (D12)
/MISTER: R5.2, U1.25 (D27)
/MISTER_NEG: MISTER_1.2 (GND), Q2.2 (D)
/POWER_BUTTON: PWR_BUTTON1.1, U1.5 (D4)
/PUMP_1: R1.2, U1.21 (D32)
/PUMP_2: R7.2, U1.22 (D33)
/PUMP_NEG_1: PUMP_1.2 (GND), Q1.2 (D)
/PUMP_NEG_2: D1.2 (A), PUMP_2.2 (GND), Q4.2 (D)
/WATER_LEV: U1.26 (D14), WATER_1.3 (DOUT)
/WiFi_BUTTON: U1.4 (D2), WIFI1.1
GND: C1_0402_100nF1.1, DHT_1.3 (GND), LCD_1.2 (GND), LED_STRIP1.3 (GND), MISC1.2, PWR1.2, PWR_BUTTON1.2, PWR_DAISY1.2, Q1.3 (S), Q2.3 (S), Q3.3 (S), Q4.3 (S), R2.1, R4.2, R6.1, R8.1, U1.2 (GND), U1.29 (GND), WATER_1.2 (GND), WIFI1.2
unnamed: Q1.1 (G), R1.1, R2.2
unnamed: Q2.1 (G), R5.1, R6.2
unnamed: Q3.1 (G), R3.2, R4.1
unnamed: Q4.1 (G), R7.1, R8.2
VCC: C1_0402_100nF1.2, D1.1 (K), DHT_1.1 (VDD), FAN1.1 (+), LCD_1.1 (VCC), LED_STRIP1.1 (VCC), MISTER_1.1 (VCC), PUMP_1.1 (VCC), PUMP_2.1 (VCC), PWR1.1, PWR_DAISY1.1, U1.30 (VIN), WATER_1.1 (VCC)

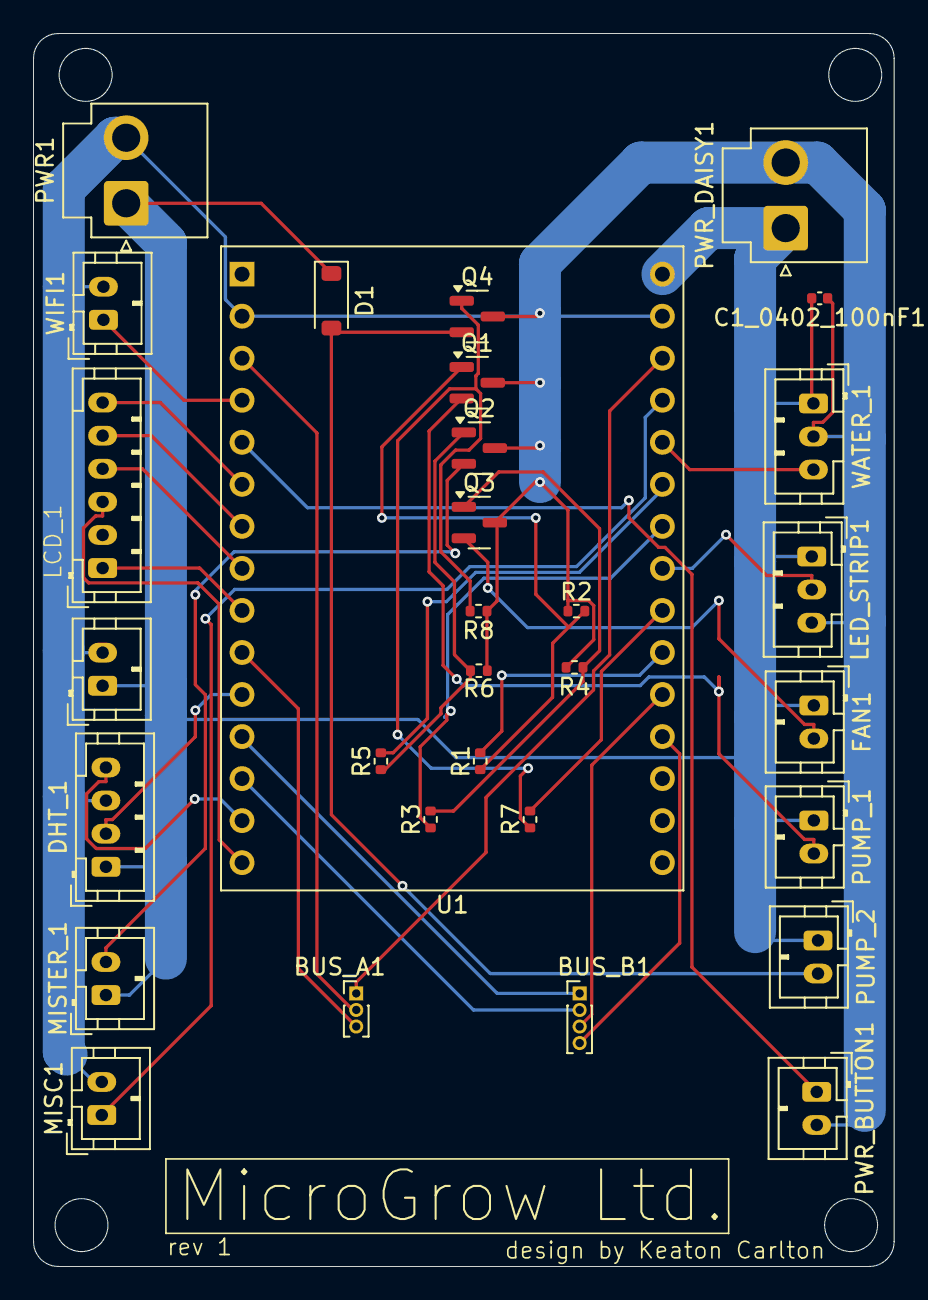
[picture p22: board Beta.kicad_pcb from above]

Board: 2 copper layers, 52.0 x 74.5 mm, 30 parts (0 on the bottom side), 33 nets.

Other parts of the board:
BUS_A1: Conn_01x03; PinHeader_1x03_P1.00mm_Vertical
BUS_B1: Conn_01x04; PinHeader_1x04_P1.00mm_Vertical

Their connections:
/A_1: BUS_A1.1; also elsewhere on the board
/A_2: BUS_A1.2; also elsewhere on the board
/A_3: BUS_A1.3; also elsewhere on the board
/B_1: BUS_B1.1; also elsewhere on the board
/B_2: BUS_B1.2; also elsewhere on the board
/B_3: BUS_B1.3; also elsewhere on the board
/B_4: BUS_B1.4; also elsewhere on the board

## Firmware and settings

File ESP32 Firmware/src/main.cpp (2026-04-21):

#include <Arduino.h>
#include "config/pins.h"
#include "config/config.h"
#include "hardware/sensors.h"
#include "hardware/actuators.h"
#include "hardware/display.h"
#include "control/scheduler.h"
#include "control/automation.h"
#include "network/wifi_manager.h"
#include "network/mqtt_client.h"
#include "storage/persistence.h"

// Global pointers - initialized in setup()
SensorManager *sensors = nullptr;
ActuatorManager *actuators = nullptr;
DisplayManager *display = nullptr;
Scheduler *scheduler = nullptr;
AutomationController *automation = nullptr;
EspWiFiManager *wifiMgr = nullptr;
PersistenceManager *storage = nullptr;
MQTTClient *mqttClient = nullptr;

// ISR for WiFi reset button
volatile bool resetWiFiRequested = false;

void IRAM_ATTR handleResetButton()
{
    resetWiFiRequested = true;
}

// FreeRTOS Tasks
void sensorTask(void *param);
void actuatorTask(void *param);
void scheduleTask(void *param);
void networkTask(void *param);

// Helpers

// Apply a fully-loaded DeviceConfig to all subsystems and schedule callbacks.
// Called both at boot (from NVS) and when a fresh /init arrives over MQTT.
static void applyConfig(const DeviceConfig &config)
{
    automation->setTargets(config.targetTemp, config.targetHumidity);
    automation->enable();

    scheduler->getLightSchedule().setTiming(
        Timing(config.lightStartSec, config.lightDurationSec, config.lightIntervalSec));
    scheduler->getWaterSchedule().setTiming(
        Timing(config.waterStartSec, config.waterDurationSec, config.waterIntervalSec));

    display->setGreenType(config.greenType);
    display->setGrowth(config.growth);

    scheduler->getWaterSchedule().enable();
    scheduler->getLightSchedule().enable();
    if (config.blackout)
        scheduler->getLightSchedule().pause();
}

static void initializeHardware()
{
    Serial.println("Creating display...");
    display = new DisplayManager();
    display->begin();
    display->showBoot();

    Serial.println("Creating sensors...");
    sensors = new SensorManager();
    sensors->begin();

    Serial.println("Creating actuators...");
    actuators = new ActuatorManager();
    actuators->begin();

    Serial.println("Creating scheduler...");
    scheduler = new Scheduler();

    Serial.println("Creating automation...");
    automation = new AutomationController(*sensors, *actuators);

    Serial.println("Creating storage...");
    storage = new PersistenceManager();

    Serial.println("Creating WiFi manager...");
    wifiMgr = new EspWiFiManager();
}

static void setupWiFiButton()
{
    pinMode(PIN_WIFI_BUTTON, INPUT_PULLUP);
    attachInterrupt(digitalPinToInterrupt(PIN_WIFI_BUTTON), handleResetButton, FALLING);
}

static void setupScheduleCallbacks()
{
    scheduler->getWaterSchedule().setCallbacks(
        [=]()
        { actuators->getPump().on(); },
        [=]()
        { actuators->getPump().off(); });

    scheduler->getLightSchedule().setCallbacks(
        [=]()
        { actuators->getLEDs().setColor(255, 255, 255); },
        [=]()
        { actuators->getLEDs().off(); });
}

static void loadAndApplyConfig()
{
    bool configured = storage->isConfigured();
    DeviceConfig config;
    if (configured)
    {
        Serial.println("Loading saved configuration...");
        config = storage->loadConfig();
        applyConfig(config);
    }
    else
    {
        config.growth = "seed";
        Serial.println("No saved configuration - awaiting MQTT setup");
    }
}

static void setupMQTT()
{
    Serial.println("Creating MQTT client...");
    mqttClient = &MQTTClient::getInstance(wifiMgr->getDeviceId());

    mqttClient->setActuators(actuators);
    mqttClient->setScheduler(scheduler);
    mqttClient->setAutomation(automation);
    mqttClient->setDisplay(display);

    MQTTCallbacks cbs;
    cbs.onConfig = [](const DeviceConfig &cfg)
    {
        storage->saveConfig(cfg);
        applyConfig(cfg);
    };
    cbs.onGrowth = [](const String &growth)
    {
        DeviceConfig cfg = storage->loadConfig();
        cfg.growth = growth;
        storage->saveConfig(cfg);
    };
    cbs.onBlackout = [](bool blackout)
    {
        DeviceConfig cfg = storage->loadConfig();
        cfg.blackout = blackout;
        storage->saveConfig(cfg);
    };
    cbs.onDelete = []()
    { storage->clear(); };

    mqttClient->setCallbacks(cbs);

    DeviceConfig config = storage->isConfigured() ? storage->loadConfig() : DeviceConfig();
    mqttClient->begin(storage->isConfigured(), config.greenType, config.growth);
}

static void initializeWiFi()
{
    Serial.println("Starting WiFi...");
    Serial.printf("Device ID: %s\n", wifiMgr->getDeviceId().c_str());
    if (!wifiMgr->begin())
    {
        Serial.println("Starting WiFi configuration portal...");
        display->showWiFiSetup(wifiMgr->getDeviceId());
        wifiMgr->startConfigPortal();
    }
}

static void startTasks()
{
    Serial.println("Creating tasks...");
    xTaskCreatePinnedToCore(sensorTask, "Sensor", 8192, NULL, 1, NULL, 1);
    xTaskCreatePinnedToCore(actuatorTask, "Actuator", 8192, NULL, 1, NULL, 1);
    xTaskCreatePinnedToCore(scheduleTask, "Schedule", 8192, NULL, 1, NULL, 1);
    xTaskCreatePinnedToCore(networkTask, "Network", 8192, NULL, 2, NULL, 1);
}

void setup()
{
    Serial.begin(SERIAL_BAUD);
    delay(1000);
    Serial.println("\n\n=== MicroGrow Starting ===");

    initializeHardware();
    setupWiFiButton();
    setupScheduleCallbacks();
    loadAndApplyConfig();
    setupMQTT();
    initializeWiFi();

    Serial.println("Starting MQTT...");
    mqttClient->connect();

    actuators->getLEDs().flash(CRGB::Teal);
    startTasks();

    actuators->getLEDs().flash(CRGB::Green);
    Serial.println("\n=== MicroGrow Ready ===\n");
}

void loop()
{
    if (resetWiFiRequested)
    {
        resetWiFiRequested = false;
        Serial.println("WiFi reset requested");
        display->showWiFiSetup(wifiMgr->getDeviceId());
        wifiMgr->resetCredentials();
    }

    vTaskDelay(portMAX_DELAY);
}

// ============================================================================
// Tasks
// ============================================================================

void sensorTask(void *param)
{
    TickType_t lastWakeTime = xTaskGetTickCount();

    while (true)
    {
        SensorReadings readings = sensors->read();

        if (wifiMgr->isConnected() && mqttClient->isInitialized() && readings.valid)
        {
            display->showSensorData(
                readings.temperature,
                readings.humidity,
                readings.waterLevelLow);
        }

        vTaskDelayUntil(&lastWakeTime, pdMS_TO_TICKS(SENSOR_READ_INTERVAL_MS));
    }
}

void actuatorTask(void *param)
{
    TickType_t lastWakeTime = xTaskGetTickCount();

    while (true)
    {
        automation->update();
        vTaskDelayUntil(&lastWakeTime, pdMS_TO_TICKS(ACTUATOR_UPDATE_INTERVAL_MS));
    }
}

void scheduleTask(void *param)
{
    TickType_t lastWakeTime = xTaskGetTickCount();
    int retryCount = 0;
    const int maxRetries = 60;

    while (!Scheduler::isTimeValid() && retryCount < maxRetries)
    {
        Serial.println("Waiting for NTP time sync...");
        vTaskDelay(pdMS_TO_TICKS(1000));
        retryCount++;
    }

    if (!Scheduler::isTimeValid())
        Serial.println("WARNING: Scheduler starting without valid time");
    else
        Serial.println("Scheduler started with valid time");

    while (true)
    {
        scheduler->update();
        vTaskDelayUntil(&lastWakeTime, pdMS_TO_TICKS(SCHEDULE_CHECK_INTERVAL_MS));
    }
}

void networkTask(void *param)
{
    TickType_t lastWakeTime = xTaskGetTickCount();
    TickType_t lastPublish = 0;
    time_t lastReading = 0;

    configTime(TIMEZONE_OFFSET_S, DST_OFFSET_S, NTP_SERVER_1, NTP_SERVER_2);

    while (true)
    {
        if (!wifiMgr->isConnected())
        {
            display->setWiFiStatus(false);
            Serial.println("WiFi disconnected, attempting reconnect...");
            actuators->getLEDs().flash(CRGB::Orange4);
            wifiMgr->reconnect();
        }
        else
        {
            display->setWiFiStatus(true);
        }

        if (wifiMgr->isConnected())
        {
            if (!mqttClient->isConnected())
            {
                display->setMQTTStatus(false);
                mqttClient->connect();
            }
            else
            {
                display->setMQTTStatus(true);
                mqttClient->loop();

                if (mqttClient->isInitialized())
                {
                    // Periodic sensor publish
                    TickType_t now = xTaskGetTickCount();
                    if (now - lastPublish > pdMS_TO_TICKS(MQTT_PUBLISH_INTERVAL_MS))
                    {
                        SensorReadings readings = sensors->read();
                        if (readings.valid)
                        {
                            mqttClient->publishSensorData(
                                readings.temperature,
                                readings.humidity,
                                readings.waterLevelLow,
                                actuators->getLEDs().getcurrentColor());
                            lastPublish = now;
                        }
                    }

                    // Periodic NVS reading save
                    time_t now_t;
                    time(&now_t);
                    if (now_t - lastReading >= READING_SAVE_INTERVAL_S)
                    {
                        SensorReadings readings = sensors->read();
                        if (readings.valid)
                        {
                            StoredReading r;
                            r.temperature = readings.temperature;
                            r.humidity = readings.humidity;
                            r.timestamp = now_t;
                            storage->saveReading(r);
                        }
                        lastReading = now_t;
                    }
                }
            }
        }

        vTaskDelayUntil(&lastWakeTime, pdMS_TO_TICKS(20));
    }
}

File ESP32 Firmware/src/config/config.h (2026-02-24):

#pragma once

#include <Arduino.h>

// WiFi & Network
#define WIFI_TIMEOUT_MS 10000
#define WIFI_PORTAL_TIMEOUT_S 180
#define WIFI_CONNECT_RETRIES 3

// MQTT
#define MQTT_BROKER "broker.emqx.io"
#define MQTT_PORT 1883
#define MQTT_TIMEOUT_MS 10000
#define MQTT_RECONNECT_DELAY_MS 5000
#define MQTT_KEEPALIVE_S 15
#define MQTT_SOCKET_TIMEOUT_S 5
#define MQTT_PUBLISH_INTERVAL_MS 3000

// Task Configuration
#define SENSOR_READ_INTERVAL_MS 2000
#define ACTUATOR_UPDATE_INTERVAL_MS 200
#define SCHEDULE_CHECK_INTERVAL_MS 200

// Timezone (EST)
#define TIMEZONE_OFFSET_S (-5 * 3600)
#define DST_OFFSET_S 0

// NTP Servers
#define NTP_SERVER_1 "pool.ntp.org"
#define NTP_SERVER_2 "time.nist.gov"

// Display
#define TFT_WIDTH 320
#define TFT_HEIGHT 240
#define TFT_ROTATION 1
#define LED_STRIP_BRIGHTNESS 50

// Manual Override
#define MANUAL_OVERRIDE_TIMEOUT_MS 300000 // 5 minutes, 0 = no timeout

// Environmental Control Thresholds
#define HUMIDITY_HIGH_THRESHOLD 70.0f
#define HUMIDITY_MED_THRESHOLD 60.0f
#define TEMP_HIGH_THRESHOLD 85.0f

// Fan PWM levels
#define FAN_PWM_OFF 0
#define FAN_PWM_LOW 128
#define FAN_PWM_HIGH 255

// Debug
#define SERIAL_BAUD 115200

// Historical Data
#define READING_SAVE_INTERVAL_S 3

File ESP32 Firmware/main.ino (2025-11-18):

#include <DHT20.h>
#include <Adafruit_Sensor.h>
#include <Adafruit_GFX.h>
#include <Adafruit_GrayOLED.h>
#include <Adafruit_SPITFT.h>
#include <Adafruit_SPITFT_Macros.h>
#include <gfxfont.h>
#include <Adafruit_ST7735.h>
#include <Adafruit_ST7789.h>
#include <Adafruit_ST7796S.h>
#include <Adafruit_ST77xx.h>
#include <FastLED.h>
#include "defs.h"
#include <Preferences.h>
#include <SPI.h>

// Forward declaration of tasks
void mqttTask(void *);
void actuatorTask(void *);
void sensorTask(void *);
void scheduleTask(void *);

// Forward declaration of sensor/actuator functions
float readTemperature(void);
float readHumidity(void);
float readWaterLevel(void);
void ledOn(void);
void ledOff(void);
void writeFan(void *);
void pumpOn(void);
void pumpOff(void);

Shared shared;
SemaphoreHandle_t mutex;
bool initialized;
Preferences prefs;
void IRAM_ATTR handleButton(); // ISR prototype
volatile bool portalRequested = false;
CRGB leds[NUM_LEDS];
Adafruit_ST7789 tft = Adafruit_ST7789(TFT_CS, TFT_DC, TFT_RST);
DHT20 dht20;
uint8_t fan_val;
extern String habitatId;
SemaphoreHandle_t led_mutex;
bool led_state;

void initHardware() {
    // Button interrupt for config portal
    pinMode(BUTTON_PIN, INPUT_PULLUP);
    attachInterrupt(digitalPinToInterrupt(BUTTON_PIN), handleButton, FALLING);

    // Motor
    pinMode(MOTOR_PIN, OUTPUT);
    digitalWrite(MOTOR_PIN, LOW);
    shared.schedules[WATER_ID_S].actionStart = pumpOn;
    shared.schedules[WATER_ID_S].actionEnd = pumpOff;

    // Fan
    pinMode(FAN_PIN, OUTPUT);
    digitalWrite(FAN_PIN, LOW);
    shared.actuators[FAN_ID] = {.writeFunc = writeFan, .cmdData = &fan_val, .manualOverride = false, .manualTriggered = false};

    // Water-level sensor
    pinMode(WATER_LEVEL_PIN, INPUT);
    shared.sensors[WATER_LEVEL_ID].readFunc = readWaterLevel;

    // LEDs
    FastLED.addLeds<WS2812, LED_PIN, GRB>(leds, NUM_LEDS);
    FastLED.setBrightness(50);
    fill_solid(leds, NUM_LEDS, CRGB::Black);
    shared.schedules[LED_ID_S].actionStart = ledOn;
    shared.schedules[LED_ID_S].actionEnd = ledOff;


    // TFT Display
    tft.init(240, 320);
    tft.fillScreen(ST77XX_BLACK);

    // Temperature and humidity sensors
    Wire.begin();
    dht20.begin();
    shared.sensors[TEMPERATURE_ID].readFunc = readTemperature;
    shared.sensors[HUMIDITY_ID].readFunc = readHumidity;
}


void setup() {
  Serial.begin(115200);
  delay(1000);

  initHardware();

  // Create mutexes
  mutex = xSemaphoreCreateMutex();
  led_mutex = xSemaphoreCreateMutex();

  prefs.begin("microgrow", true);

  initialized = prefs.getBool("init", false);

  if (!initialized) {
      Serial.println("NVS empty");

      shared.targets_ready = false;
      shared.schedules_ready = false;

  } else {
      Serial.println("NVS loaded");

      habitatId = prefs.getString("habitatId", "");
      shared.targets.humidity    = prefs.getFloat("tHumidity", 60.0f);
      shared.targets.temperature = prefs.getFloat("tTemp", 75.0f);

      shared.schedules[LED_ID_S].startSec   = prefs.getULong("light_start", 0);
      shared.schedules[LED_ID_S].durationSec    = prefs.getULong("light_dur",   0);
      shared.schedules[LED_ID_S].intervalSec    = prefs.getULong("light_int",   0);

      shared.schedules[WATER_ID_S].startSec   = prefs.getULong("water_start", 0);
      shared.schedules[WATER_ID_S].durationSec    = prefs.getULong("water_dur",   0);
      shared.schedules[WATER_ID_S].intervalSec    = prefs.getULong("water_int",   0);

      shared.targets_ready = true;
      shared.schedules_ready = true;
  }

  prefs.end();

  // Create tasks
  xTaskCreatePinnedToCore(sensorTask, "Sensor", 4096, NULL, 1, NULL, 1);
  xTaskCreatePinnedToCore(mqttTask, "MQTT", 8192, NULL, 2, NULL, 1);
  xTaskCreatePinnedToCore(actuatorTask, "Actuator", 4096, NULL, 1, NULL, 1);
  xTaskCreatePinnedToCore(scheduleTask, "Schedule", 4096, NULL, 1, NULL, 1);
}

void loop() {
  vTaskDelay(portMAX_DELAY);  // nothing runs here
}

// ISR sets a flag to trigger the portal
void IRAM_ATTR handleButton() {
  portalRequested = true;
}

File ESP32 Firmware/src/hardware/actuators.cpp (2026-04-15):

#include "actuators.h"
#include "../config/pins.h"
#include "../config/config.h"

// ============================================================================
// Fan
// ============================================================================

Fan::Fan(uint8_t pin) : pin(pin)
{
    pinMode(pin, OUTPUT);
    digitalWrite(pin, LOW);
}

void Fan::on()
{
    if (!running)
    {
        digitalWrite(pin, HIGH);
        running = true;
        Serial.println("Fan: ON");
    }
}

void Fan::off()
{
    if (running)
    {
        digitalWrite(pin, LOW);
        running = false;
        Serial.println("Fan: OFF");
    }
}

// ============================================================================
// Water Pump
// ============================================================================

WaterPump::WaterPump(uint8_t pin) : pin(pin)
{
    pinMode(pin, OUTPUT);
    digitalWrite(pin, LOW);
}

void WaterPump::on()
{
    if (!running)
    {
        digitalWrite(pin, HIGH);
        running = true;
        Serial.println("Water Pump: ON");
    }
}

void WaterPump::off()
{
    if (running)
    {
        digitalWrite(pin, LOW);
        running = false;
        Serial.println("Water Pump: OFF");
    }
}

// ============================================================================
// Mister
// ============================================================================

Mister::Mister(uint8_t pin) : pin(pin)
{
    pinMode(pin, OUTPUT);
    digitalWrite(pin, LOW);
}

void Mister::on()
{
    if (!running)
    {
        digitalWrite(pin, HIGH);
        running = true;
        Serial.println("Mister: ON");
    }
}

void Mister::off()
{
    if (running)
    {
        digitalWrite(pin, LOW);
        running = false;
        Serial.println("Mister: OFF");
    }
}

// ============================================================================
// LED Strip
// ============================================================================

LEDStrip::LEDStrip(uint8_t pin, uint16_t numLeds) : numLeds(numLeds)
{
    leds = new CRGB[numLeds];
    FastLED.addLeds<WS2812, PIN_LED_STRIP, GRB>(leds, numLeds);
    FastLED.setBrightness(LED_STRIP_BRIGHTNESS);
    currentColor = CRGB::Black;
    fill_solid(leds, numLeds, CRGB::Black);
    FastLED.show();
}

void LEDStrip::write(uint8_t brightness)
{
    setBrightness(brightness);
    if (brightness > 0)
    {
        setColor(CRGB::White);
    }
    else
    {
        off();
    }
}

void LEDStrip::on()
{
    setColor(currentColor);
}

void LEDStrip::setColor(uint8_t r, uint8_t g, uint8_t b)
{
    setColor(CRGB(r, g, b));
}

void LEDStrip::setColor(CRGB color)
{
    currentColor = color;
    fill_solid(leds, numLeds, color);
    FastLED.show();
    ledOn = (color != CRGB::Black);

    Serial.printf("LEDs: RGB(%d,%d,%d)%s\n",
                  color.r, color.g, color.b,
                  manualOverride ? " (manual)" : "");
}

void LEDStrip::setBrightness(uint8_t brightness)
{
    FastLED.setBrightness(brightness);
    FastLED.show();
}

void LEDStrip::off()
{
    setColor(CRGB::Black);
}

void LEDStrip::flash(CRGB color)
{
    // Save current color and state
    CRGB previousColor = currentColor;
    bool wasOn = ledOn;

    // Set new color to flash
    currentColor = color;

    // Flash LEDs twice
    setColor(color);
    delay(300);
    off();
    delay(300);

    setColor(color);
    delay(300);
    off();
    delay(300);

    // Restore previous color
    setColor(previousColor);

    // Restore previous state
    if (wasOn)
    {
        on();
    }
}

// ============================================================================
// Actuator Manager
// ============================================================================

ActuatorManager::ActuatorManager()
    : fan(PIN_FAN), pump(PIN_WATER_PUMP), mister(PIN_MISTER), leds(PIN_LED_STRIP, NUM_LEDS)
{
}

bool ActuatorManager::begin()
{
    Serial.println("Actuators initialized");
    return true;
}

void ActuatorManager::allOff()
{
    fan.off();
    pump.off();
    mister.off();
    leds.off();
    Serial.println("All actuators turned OFF");
}

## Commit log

2025-10-22 Creates MQTT functionality, demonstrates ADC, PWM
    Useful for demonstration of key features
2025-10-25 Fixed merge for main, going to switch to new branch to develop
2025-10-26 initial app state with a Habitat class to keep track of each Micro-Grow habitat
2025-10-26 Remade app_state and added database.dart to keep track of persistent data locally with Hive
2025-10-26 revamped MQTT to be its own class. Made connect() its own function. added and tested a setupHabitat to init an ESP32. added sensorSubscribe to tap into ESP32 sensor topic.
2025-10-26 sensor subscribe didn't get added with last commit
2025-10-26 sensor data viewing screen with MQTT functionality to subscribe to selected habitat id sensor topic
2025-10-27 Refactor MQTT and sensor integration
    Updated WiFi and MQTT connection details, added DHT sensor support, and improved message handling.
2025-10-27 Update README with project details and future plans
    Expanded README with prototype details, features, bugs, and future improvements.
2025-11-04 added debug button that clears habitats. Also made it so that multiple habitats can be shown.
2025-11-13 added button to delete habitats on UI side
2025-11-15 There's a decent amount of small changes kinda lost track oops. Most recent is getting current time to send to esp32 for scheduling
2025-11-15 Sensor screen UI update
2025-11-16 Added all STLs
    [Back Plate V1.stl, Base Component V2.stl, Base Component V3.stl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]
2025-11-17 STL file and screenshots of 3D model
    [Base Component V4.stl]
2025-11-17 Update README to specify pre-alpha and design prototype features
    Updated README to reflect pre-alpha build features and design prototype details.
2025-11-17 made small MQTT init fix to break up init messages so ESP32 can parse easily
2025-11-17 led override any color
2025-11-18 Publish led state
2025-11-18 light control for LED override
2025-11-18 Improved sensor reading screen
2025-11-18 Fixed Water level sensor parsing
2025-11-18 edited pins and fixed stuff
    [actuators.ino, defs.h, main.ino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]
2025-11-18 fixed humidity
    made DHT20 read only once. Fixes the routine of getting temp + humidity. Required a file scope "status" variable for DHT20 for minimal changes to structure.
    [sensors.ino]
2025-11-18 Added platformIO IDE functionality to ESP32 Firmware
    Easiest way to use this is to install the platformIO extension on VS code and build/upload to the DevKit
2026-01-31 Create PCB folder
2026-01-31 Uploaded Alpha Build PCB Schematic, Layout
    [prototype.kicad_sch]
2026-01-31 Sorry for a massive dump instead of smaller commits of files but I change them all so much because I mess up that I thought I'd just send them all when done. MAde water reservoir from ground up, took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
    [Back Plate V1.stl, Base Component V1.stl, Base Component V2.stl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]
2026-02-05 DHT sensor fixed and got rid of old Arduino stuff. Also improved scheduler and made esp actaully used the saved configuration
    [actuators.cpp, actuators.ino, config.h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]
2026-02-07 added pcb updates
    [prototype.kicad_sch]
2026-02-07 updated schematic dates/details
2026-02-09 uploaded revision of pcb
2026-02-11 Tried to implement coin system for harvesting microgreens. Works, but not sure I like the current architecture for expanding. Gonna plan it out more then continue
2026-02-12 Realized there was no tolerance for many components, and the way I made everything made that annoying to fix. Also had to change the base for the new LCD screen size, which I also made extremely diff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
    [Base Component V1.stl, Buttons V1.stl, Leaf Door Holder V1.stl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]
2026-02-12 Attempt 2 at door changes
    [Front DoorV1.stl]
2026-02-14 pcb revision
    [Beta-B_Cu.gbl, Beta-B_Cu.gbr, Beta-B_Mask.gbr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]
2026-02-19 Preliminary past sensor readings. I need to add functionality to save it to Hive database but it already took longer than expected so will do that later.
2026-02-20 Added functionality so that sensor data is saved and displayed properly
2026-02-20 added a feature that allows for a graphical representation of temp and humidity from past sensor logs from moment of habitat creation
2026-02-21 Remodeled the garden section, now called greenhouse section. Made it so that habitats, upon creation, are entered into a 2x3 grid that represents the physical configuration (will make it customizable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
2026-02-24 Made it so that growht is tracked incrementally now. also made it so that game reflects this with cute pngs
    [Back Plate V1.3mf, Base.3mf, Front Door V1.3mf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]
2026-02-25 Implement logic for LED feedback
2026-02-26 Add automation function to drive LED feedback
2026-03-13 Fix conflict with pump manual override and water schedule
    [mqtt_client.cpp]
2026-03-25 Added blackout periods as a possible plant feature. Made it so that it is kept tracked such as reservoir or harvest ready. Also, made it so that it is published to MQTT when over so that ESP32 can re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
2026-03-25 Made blackout MQTT message be retained just in case habitat is off
2026-03-26 Configure setup for sending local push notifications to Android device
2026-04-15 refactored approach to persistence manager and implemented water pump pulse
